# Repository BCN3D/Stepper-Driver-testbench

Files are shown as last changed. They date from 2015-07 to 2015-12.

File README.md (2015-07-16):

# Stepper Driver Test Bench
Electronics Test Bench used for testing and callibrating the Stepper drivers for the BCN3D Sigma.
It's based on a Pogo bed system where the bottom board has the components and the other two boards serve as support for
the board to test (Stepper driver).

Basically it's made for callibrating the power of the DRV8825 based Stepper drivers used in the BCND3D Sigma and testing them out
with a real motor.

It uses capacitive touch sensor instead of mechanical switches as it will be used a lot...
We were inspired by the awesome tutorial by [Sparkfun](https://learn.sparkfun.com/tutorials/constant-innovation-in-quality-control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)

##Code
Implements the [AccelStepper](http://www.airspayce.com/mikem/arduino/AccelStepper/) Library and [Capacitive Sensor Library](http://playground.arduino.cc/Main/CapacitiveSensor?from=Main.CapSense).

One button conmutes the 24 Volt in from the power supply to avoid shorts and the other button starts a motor routine to test
the motor.

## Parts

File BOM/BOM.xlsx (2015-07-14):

Qty | Value | Device | Package | Parts | Description | BOM | PROD_ID | VALUE
1 |  | CRYSTALHC49US | HC49US | Y1 | Various standard crystals. Proven footprints.
1 |  | JST_2PIN-SMT-RA | JST-PH-2-SMT-RA | JST | JST 2-Pin Connectors of various flavors
1 |  | LEDCHIP-LED0805 | CHIP-LED0805 | LED1 | LED
2 |  | LEDCHIPLED_0805 | CHIPLED_0805 | LED4, LED5 | LED
3 |  | LEDCHIPLED_1206 | CHIPLED_1206 | HIGH, LOW, OK | LED
15 |  | PINHD-1X1 | 1X01 | SCREW, JP2, JP3, JP4, JP5, JP6, JP7, JP8, JP9, JP10, JP11, JP12, JP13, JP14, JP15 | Pin header 1x1 for 0.1 spacing"
1 |  | PINHD-1X4 | 1X04 | MOTOR | PIN HEADER
1 |  | PINHD-1X8 | 1X08 | PORTC | PIN HEADER
16 |  | R-US_M0805 | M0805 | R1, R2, R3, R4, R11, R12, R13, R14, R15, R16, R17, R18, R27, R28, R29, R30 | RESISTOR, American symbol
2 |  | SWITCH-SPDTKIT | SWITCH-SPDT_KIT | S1, S2 | SPDT Switch |  | SWCH-08261
1 | +5V | V_REG_78XX7812 | TO-252 | U1 | Voltage Regulator |  | VREG-12370 | +12v
1 | 0.33uF | C-USC0805 | C0805 | C3 | CAPACITOR, American symbol
1 | 100 | R-US_M0805 | M0805 | R22 | RESISTOR, American symbol
8 | 100n | C-USC0805 | C0805 | C1, C5, C6, C7, C8, C9, C12, C13 | CAPACITOR, American symbol
1 | 100uF | CPOL-USUD-8X10 | UD-8X10_NICHICON | C4 | POLARIZED CAPACITOR, American symbol
3 | 10K | R-US_M0805 | M0805 | R9, R21, R23 | RESISTOR, American symbol
2 | 10M | R-US_M0805 | M0805 | R19, R20 | RESISTOR, American symbol
4 | 1K | R-US_M0805 | M0805 | R5, R6, R10, R31 | RESISTOR, American symbol
1 | 1uF | C-USC0805 | C0805 | C2 | CAPACITOR, American symbol
2 | 22p | C-USC0805 | C0805 | C10, C11 | CAPACITOR, American symbol
2 | 5.6K | R-US_M0805 | M0805 | R24, R25 | RESISTOR, American symbol
3 | 68.1K | R-US_M0805 | M0805 | R7, R8, R26 | RESISTOR, American symbol
1 | 74HC4052 | 74HC4052SO | SO16 | U2 | Dual 4:1 analog mux |  | IC-09813 | 74HC4052
1 | ATMEGA328P | ATMEGA328P_TQFP | TQFP32-08 | U3 |  |  | IC-09069 | ATMEGA328P_TQFP
1 | AVR_SPI_PRG_6PTH | AVR_SPI_PRG_6PTH | 2X3 | ICSP | AVR ISP 6 Pin
2 | CAPSENSE_PAD | CAPSENSE_PAD | CAPSENSE_PAD | U$1, U$2 | Generic copper pad for a capacitive touch sensor.
1 | FTDI_BASICPTH | FTDI_BASICPTH | FTDI_BASIC | FTDI | FTDI Basic header with labels
1 | LM339D | LM339D | SO14 | IC2 | Low Power Low Offset Voltage Quad Comparators
1 | MMBT2222A | TRANSISTOR_NPNMMBT2222A | SOT23-3 | Q2 | Generic NPN BJT |  | TRANS-08049 | MMBT2222A
1 | MOSFET-PCHANNELFQP27P06 | MOSFET-PCHANNELFQP27P06 | TO220V | Q3 | Generic PMOSFET
1 | POWER_JACKPTH | POWER_JACKPTH | POWER_JACK_PTH | JP1 | Power Jack |  | CONN-08197
1 | SHORTT5 | SHORTT5 | SHORT_TOP-50 | SH1 | Short between two nets | no
1 | SPST_TACT-EVQQ2 | SPST_TACT-EVQQ2 | EVQ-Q2 | RESET | SMT 6mm switch, EVQQ2 series
1 | USB+SHIELD | USB+SHIELD | USB-B-PTH | U$3 | USB+Shield

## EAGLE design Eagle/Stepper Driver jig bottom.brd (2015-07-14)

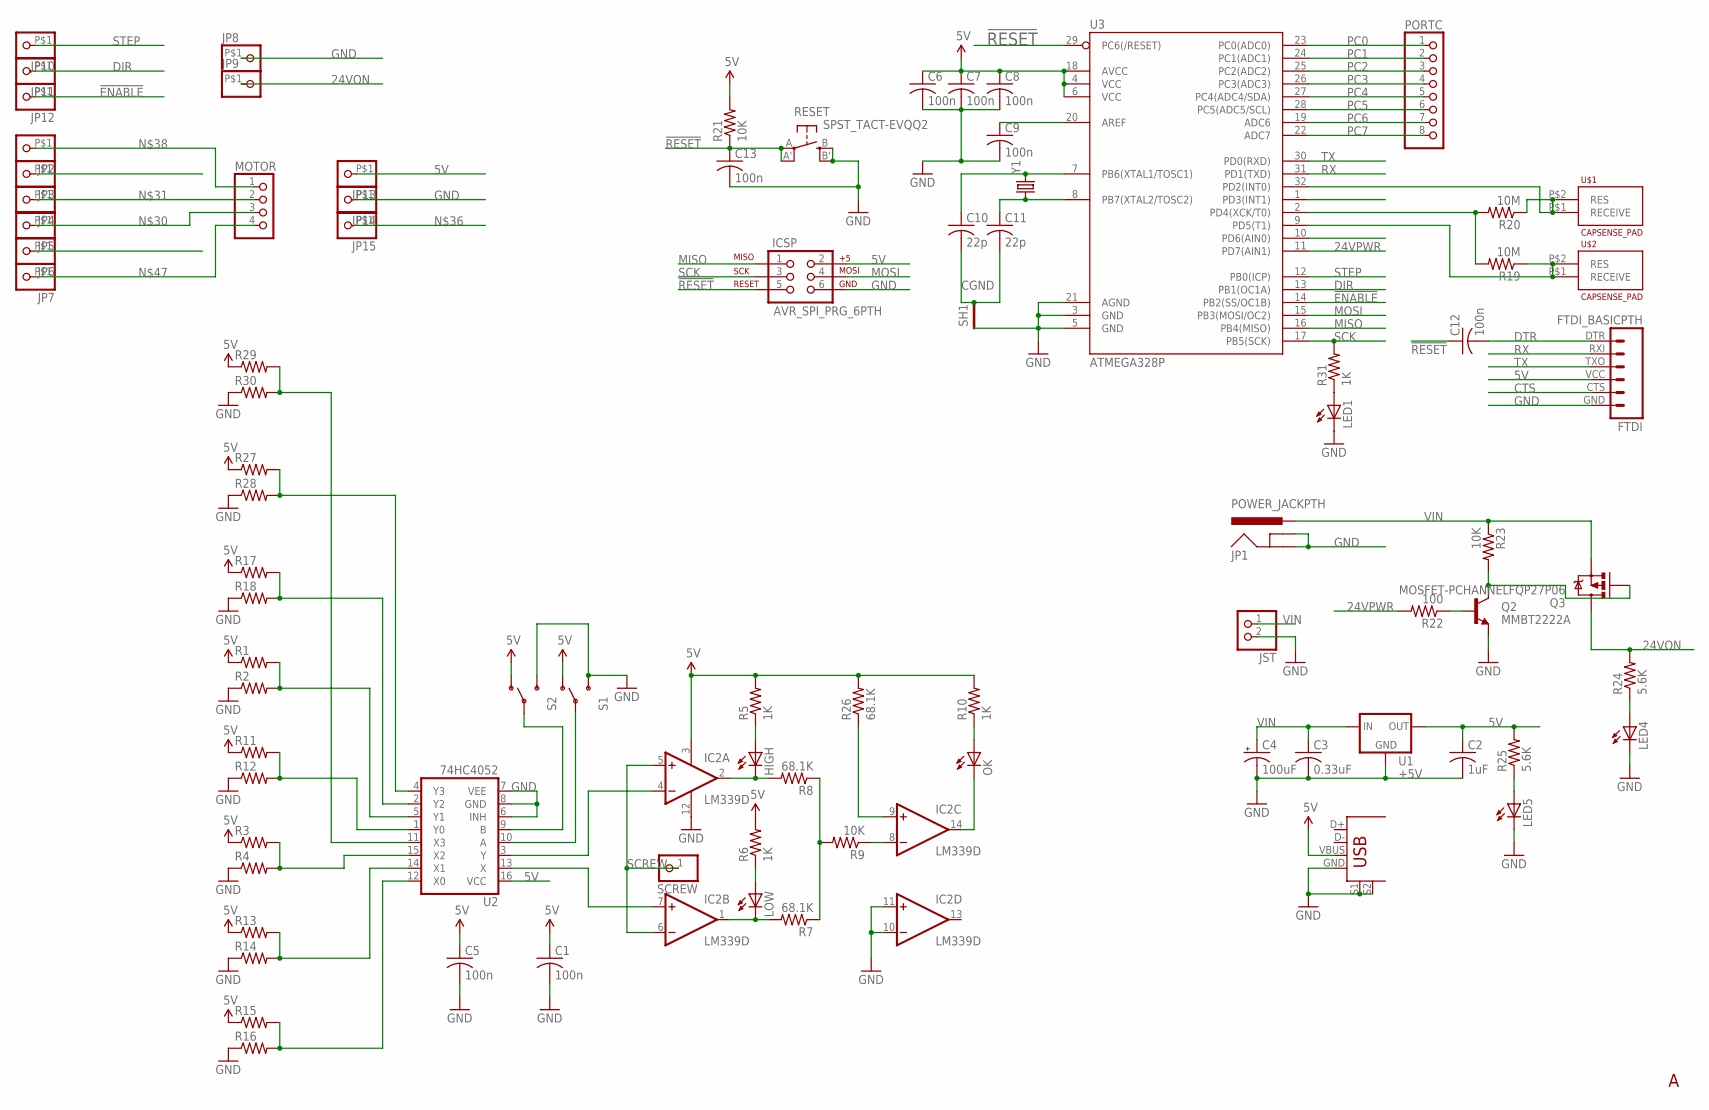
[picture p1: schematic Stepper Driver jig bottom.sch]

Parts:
C1, C5, C6, C7, C8, C9, C12, C13: 100n; C0805
C2: 1uF; C0805
C3: 0.33uF; C0805
C4: 100uF; UD-8X10_NICHICON
C10, C11: 22p; C0805
FTDI: FTDI_BASICPTH; FTDI_BASIC
HIGH: LEDCHIPLED_1206; CHIPLED_1206
IC2: LM339D; SO14
ICSP: AVR_SPI_PRG_6PTH; 2X3
JP1: POWER_JACKPTH; POWER_JACK_PTH
JP2, JP3, JP4, JP5, JP6, JP7, JP8, JP9, JP10, JP11, JP12, JP13, JP14, JP15: PINHD-1X1; POGOPIN
JST: JST_2PIN-SMT-RA; JST-PH-2-SMT-RA
LED1: LEDCHIP-LED0805; CHIP-LED0805
LED4, LED5: LEDCHIPLED_0805; CHIPLED_0805
LOW: LEDCHIPLED_1206; CHIPLED_1206
MOTOR: PINHD-1X4; 1X04
OK: LEDCHIPLED_1206; CHIPLED_1206
PORTC: PINHD-1X8; 1X08
Q2: MMBT2222A; SOT23-3
Q3: MOSFET-PCHANNELFQP27P06; TO220V
R1, R2, R3, R4, R11, R12, R13, R14, R15, R16, R17, R18, R27, R28, R29, R30: R-US_M0805; M0805
R5, R6, R10, R31: 1K; M0805
R7, R8, R26: 68.1K; M0805
R9, R21, R23: 10K; M0805
R19, R20: 10M; M0805
R22: 100; M0805
R24, R25: 5.6K; M0805
RESET: SPST_TACT-EVQQ2; EVQ-Q2
S1, S2: SWITCH-SPDTKIT; SWITCH-SPDT_KIT
SCREW: PINHD-1X1; 1X01
SH1: SHORTT5; SHORT_TOP-50
U1: +5V; TO-252
U2: 74HC4052; SO16
U3: ATMEGA328P; TQFP32-08
U$1, U$2: CAPSENSE_PAD
U$3: USB+SHIELD; USB-B-PTH
Y1: CRYSTALHC49US; HC49US

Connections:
5V: C1.1, C2.1, C5.1, C6.1, C7.1, C8.1, FTDI.VCC (4), IC2.3 (V+), ICSP.2, JP13.P$1, R1.1, R3.1, R5.2, R6.2, R10.2, R11.1, R13.1, R15.1, R17.1, R21.2, R25.2, R26.2, R27.1, R29.1, S1.1 (O), S2.1 (O), U1.2 (OUT), U2.16 (VCC), U3.4 (VCC), U3.6 (VCC), U3.18 (AVCC), U$3.VBUS
24VON: JP9.P$1, Q3.2 (D), R24.2
24VPWR: R22.2, U3.11 (PD7(AIN1))
!ENABLE: JP12.P$1, U3.14 (PB2(SS/OC1B))
!RESET: C12.1, C13.1, ICSP.5, R21.1, RESET.A, RESET.A' (P1), U3.29 (PC6(/RESET))
CGND: C10.2, C11.2, SH1.2
CTS: FTDI.CTS (5)
DIR: JP11.P$1, U3.13 (PB1(OC1A))
DTR: C12.2, FTDI.DTR (1)
GND: C1.2, C2.2, C3.2, C4.-, C5.2, C6.2, C7.2, C8.2, C9.2, C13.2, FTDI.GND (6), IC2.10 (-IN), IC2.11 (+IN), IC2.12 (GND), ICSP.6, JP1.GND, JP1.GNDBREAK, JP8.P$1, JP14.P$1, JST.2 (1), LED1.C, LED4.C, LED5.C, Q2.2 (E), R2.1, R4.1, R12.1, R14.1, R16.1, R18.1, R28.1, R30.1, RESET.B (S), RESET.B' (S1), S1.3 (S), S2.3 (S), SH1.1, U1.3 (GND), U2.6 (INH), U2.7 (VEE), U2.8 (GND), U3.3 (GND), U3.5 (GND), U3.21 (AGND), U$3.GND, U$3.S1, U$3.S2
MISO: ICSP.1, U3.16 (PB4(MISO))
MOSI: ICSP.4, U3.15 (PB3(MOSI/OC2))
unnamed: IC2.4 (-IN), U2.3 (Y)
unnamed: IC2.7 (+IN), U2.13 (X)
unnamed: IC2.1 (OUT), LOW.C, R7.2
unnamed: LOW.A, R6.1
unnamed: HIGH.C, IC2.2 (OUT), R8.2
unnamed: HIGH.A, R5.1
unnamed: R7.1, R8.1, R9.2
unnamed: IC2.8 (-IN), R9.1
unnamed: OK.A, R10.1
unnamed: IC2.14 (OUT), OK.C
unnamed: R11.2, R12.2, U2.1 (Y0)
unnamed: R1.2, R2.2, U2.5 (Y1)
unnamed: R3.2, R4.2, U2.15 (X2)
unnamed: R13.2, R14.2, U2.14 (X1)
unnamed: R15.2, R16.2, U2.12 (X0)
unnamed: R17.2, R18.2, U2.2 (Y2)
unnamed: S1.2, U2.10 (A)
unnamed: S2.2, U2.9 (B)
unnamed: R19.1, U3.9 (PD5(T1)), U$2.P$1 (RECEIVE), U$2.P$2 (RES)
unnamed: C11.1, U3.8 (PB7(XTAL2/TOSC2)), Y1.1
unnamed: C9.1, U3.20 (AREF)
unnamed: C10.1, U3.7 (PB6(XTAL1/TOSC1)), Y1.2
unnamed: Q2.3 (C), Q3.1 (G), R23.2
unnamed: Q2.1 (B), R22.1
unnamed: R19.2, R20.2, U3.2 (PD4(XCK/T0))
unnamed: R20.1, U3.32 (PD2(INT0)), U$1.P$1 (RECEIVE), U$1.P$2 (RES)
unnamed: JP5.P$1, MOTOR.3
unnamed: JP4.P$1, MOTOR.2
unnamed: JP2.P$1, MOTOR.1
unnamed: LED4.A, R24.1
unnamed: LED5.A, R25.1
unnamed: JP7.P$1, MOTOR.4
unnamed: IC2.9 (+IN), R26.1
unnamed: R27.2, R28.2, U2.4 (Y3)
unnamed: R29.2, R30.2, U2.11 (X3)
unnamed: LED1.A, R31.1
PC0: PORTC.1, U3.23 (PC0(ADC0))
PC1: PORTC.2, U3.24 (PC1(ADC1))
PC2: PORTC.3, U3.25 (PC2(ADC2))
PC3: PORTC.4, U3.26 (PC3(ADC3))
PC4: PORTC.5, U3.27 (PC4(ADC4/SDA))
PC5: PORTC.6, U3.28 (PC5(ADC5/SCL))
PC6: PORTC.7, U3.19 (ADC6)
PC7: PORTC.8, U3.22 (ADC7)
RX: FTDI.RXI (2), U3.31 (PD1(TXD))
SCK: ICSP.3, R31.2, U3.17 (PB5(SCK))
SCREW: IC2.5 (+IN), IC2.6 (-IN), SCREW.1
STEP: JP10.P$1, U3.12 (PB0(ICP))
TX: FTDI.TXO (3), U3.30 (PD0(RXD))
VIN: C3.1, C4.+, JP1.PWR, JST.1 (2), Q3.3 (S), R23.1, U1.1 (IN)

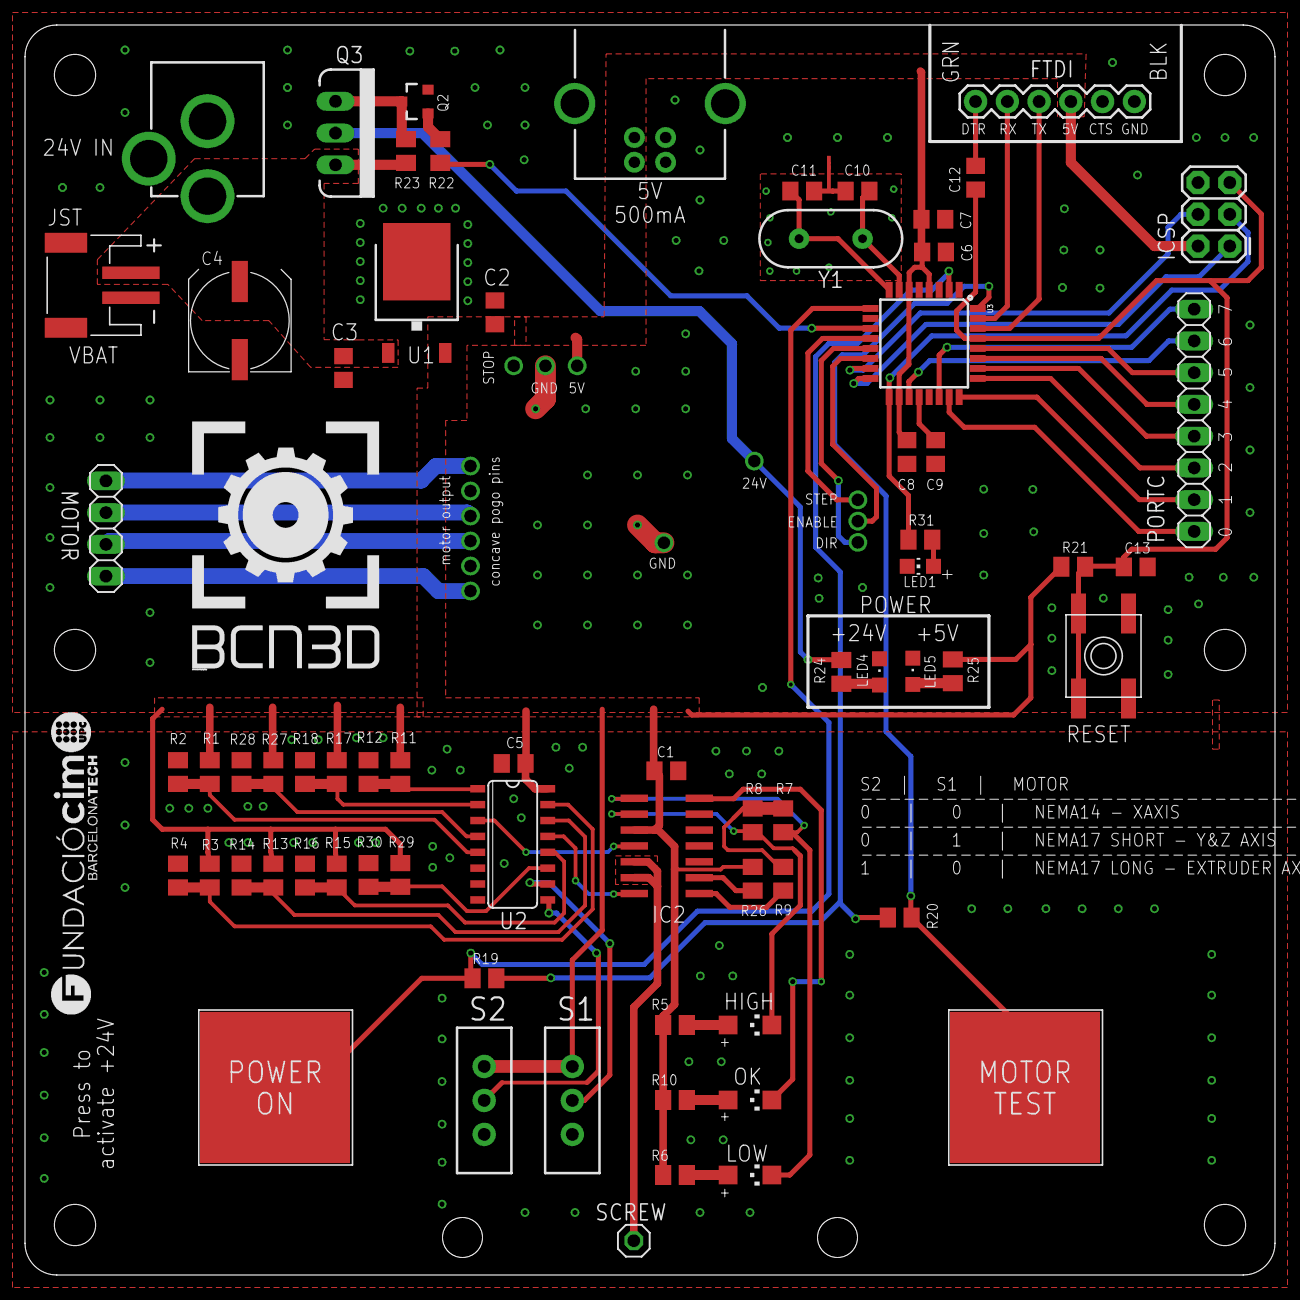
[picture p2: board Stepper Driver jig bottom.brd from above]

Board: 2 copper layers, 100.0 x 100.0 mm, 93 parts (0 on the bottom side), 61 nets.

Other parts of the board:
U$4, U$5, U$6, U$7, U$8, U$9: STAND-OFF
U$10: FCIM_LOGO
U$11: BCN3D_LOGO

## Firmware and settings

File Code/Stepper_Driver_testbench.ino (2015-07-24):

/*-------------------------------------------------
Stepper Driver test bench

BCN3D Technologies - Fundacio CIM
Marc Cobler - July 2015

This sketch is used in the Stepper driver test bench
It consist in 2 capacitive touch buttons that activates
different routines. 

The purpose is to callibrate the stepper drivers and test
them out with a turning motor.

---------------------------------------------------*/
#include <CapacitiveSensor.h>
#include <AccelStepper.h>
//--------CONSTANTS------------------
#define SENSORPOWER 5
#define SENSORMOTOR 2
#define SENDPIN 4

#define LED 13
#define STEP 8
#define DIR 9
#define EN 10

#define POWER 7

#define THRESHOLD 3800	//Threshold for the capacitive Sensor pins
#define MAXSPEED 1000

//--------VARIABLES-----------------
unsigned long csSum1, csSum2;
bool powerState;

CapacitiveSensor motorTest = CapacitiveSensor(SENDPIN, SENSORMOTOR);	//
CapacitiveSensor powerOn = CapacitiveSensor(SENDPIN, SENSORPOWER);		//

AccelStepper stepper(AccelStepper::DRIVER, STEP, DIR);
void setup()
{
	powerState = false;		//24V turned off at beginning
	pinMode(STEP, OUTPUT);
	pinMode(DIR, OUTPUT);
	pinMode(EN, OUTPUT);
	pinMode(LED, OUTPUT);
	
	Serial.begin(115200);
	Serial.println("Starting the Stepper Driver test bench...");

	stepper.setMaxSpeed(MAXSPEED);
	stepper.setEnablePin(EN);
	stepper.disableOutputs();
	stepper.moveTo(500);
}

void loop()
{
	CSMotor();
	CSPower();

}
//----------USER FUNCTIONS-----------------
void CSMotor() {
	long cs = motorTest.capacitiveSensor(80); //a: Sensor resolution is set to 80
	if (cs > 100) { //b: Arbitrary number
		csSum1 += cs;
		Serial.println(cs);
		if (csSum1 >= THRESHOLD) //c: This value is the threshold, a High value means it takes longer to trigger
		{
			moveMotor();
			turnLed();
			Serial.print("Trigger Motor Test Button: ");
			Serial.println(csSum1);
			if (csSum1 > 0) { csSum1 = 0; } //Reset
			motorTest.reset_CS_AutoCal(); //Stops readings
		}
		} else {
		csSum1 = 0; //Timeout caused by bad readings
	}
	
}
void CSPower() {
	long cs = powerOn.capacitiveSensor(80); //a: Sensor resolution is set to 80
	if (cs > 100) { //b: Arbitrary number
		csSum2 += cs;
		Serial.println(cs);
		if (csSum2 >= THRESHOLD) //c: This value is the threshold, a High value means it takes longer to trigger
		{
			conmute24V();
			turnLed();
			Serial.print("Trigger Power Button: ");
			Serial.println(csSum2);
			if (csSum2 > 0) { csSum2 = 0; } //Reset
			powerOn.reset_CS_AutoCal(); //Stops readings
		}
		} else {
		csSum2 = 0; //Timeout caused by bad readings
	}
	
}
void moveMotor() {
	if (stepper.distanceToGo() == 0)
		stepper.moveTo(-stepper.currentPosition());
		
	stepper.run();
}

void conmute24V() {
	if (powerState)
	{
		Serial.println("24V ON");
		digitalWrite(POWER, HIGH);
	} else {
		Serial.println("24V OFF");
		digitalWrite(POWER, LOW);
	}
	
	powerState = !powerState; 
}

void turnLed() {
	digitalWrite(LED, HIGH);
	delay(5);
	digitalWrite(LED, LOW);
}

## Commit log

2015-07-14 First version of the Stepper driver test bench board
    All the documentation needed for replicating the Stepper driver test
    bench. Version 1.0 REV_A.
    Sent to Fab House
    I'll be uploading the code soon.
    [BOM.xlsx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]
2015-07-24 Indicator LED function
    Now when you press a capacitive button, an led flashes for 5 ms to give
    some feedback.
2015-12-02 Reorder file tree
    new eagle folder
    [Stepper Driver jig bottom.brd, Stepper Driver jig bottom.sch, Stepper Driver jig middle.brd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]

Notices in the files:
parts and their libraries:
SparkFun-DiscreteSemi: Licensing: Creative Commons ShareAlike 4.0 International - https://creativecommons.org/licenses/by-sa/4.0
